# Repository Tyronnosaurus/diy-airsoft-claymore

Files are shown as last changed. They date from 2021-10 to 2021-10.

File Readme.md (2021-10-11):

# DIY Airsoft claymore

## About

This is a remote controlled, motion sensing, BB throwing airsoft Claymore that I developed, built and used on my own matches.
I'm releasing its design on the hope that other makers can enjoy it.

More info and some videos @ https://airsoftdiy.com/3d-printed-airsoft-claymore/

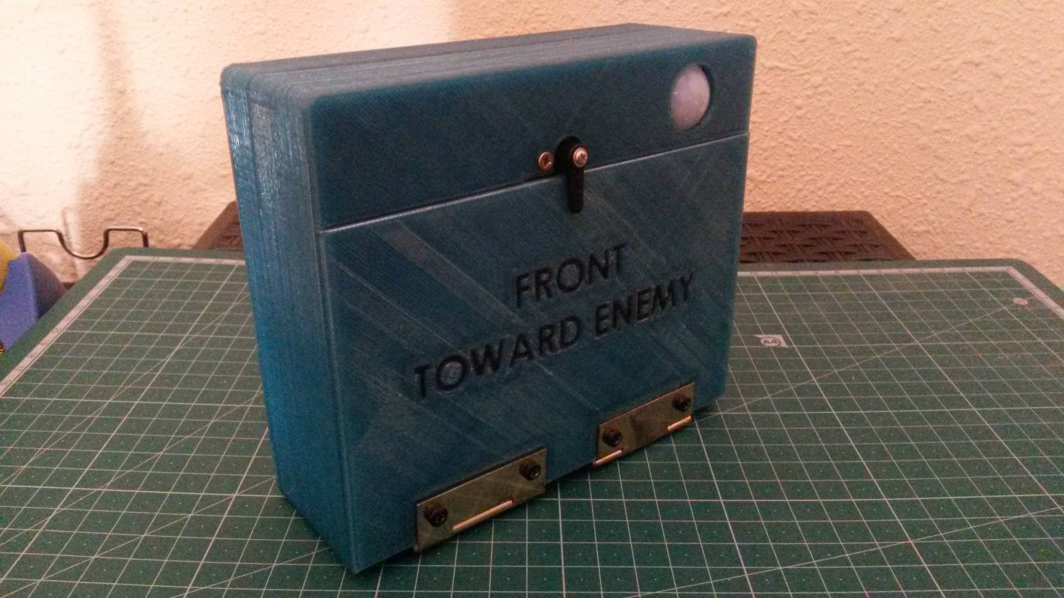
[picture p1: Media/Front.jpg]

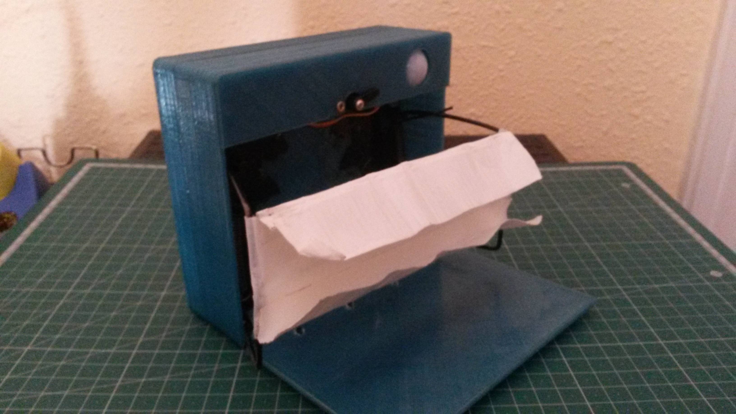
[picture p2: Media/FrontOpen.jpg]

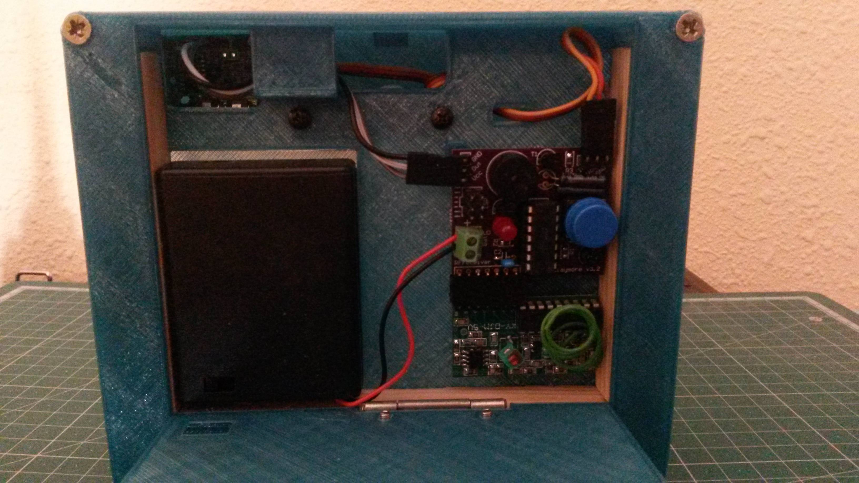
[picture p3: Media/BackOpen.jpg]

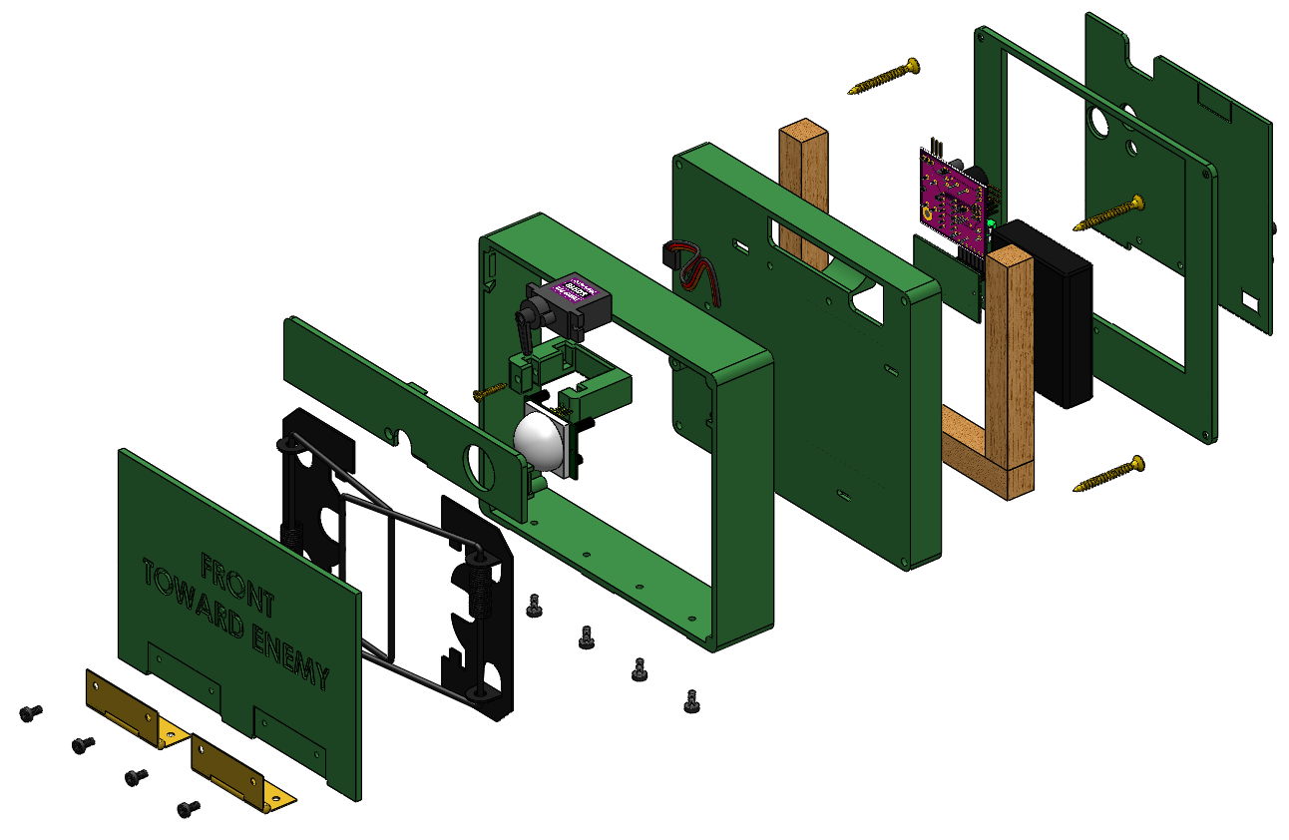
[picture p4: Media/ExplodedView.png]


## Features (for users)
- A doble mousetrap mechanism that shoots BBs forward.
- A motion sensor that triggers when an enemy (or a friend, or you) walks in front.
- Flashing Led and loud piezo in case the victim doesn't realize what hit him.
- A button on the backside to open/close (short press) or activate/deactivate the motion sensor (long press).
- A remote controller with these functions (note the bold initials, which correspond to the remote buttons):
	- **A**ctivate the motion sensor.
	- **B**OOM -> Immediately opens and shoots the BBs.
	- **C**heck range -> Flash Led. Useful if you hide far and aren't sure if the signal will reach. If it's too sunny to see the Led, a long press will also trigger a sound. 
	- **D**eactivate the motion sensor.
- Works on 4xAAA batteries. Very long battery life. While it's not opening or closing, it sleeps and only consumes a few microamperes (even while motion sensor is active).

## Features (for makers)
- Easy to print body. All parts have a flat surface and need no supports.
- Most of the structural integrity comes from 3 internal wood bars. Otherwise it would literally self-destruct due to the force of the rat trap springs.
- Easy to solder PCB. Most components are big and through-hole, with a couple SMD resistors but they're still relatively big.

## Instructions
**At the moment there is no step-by-step tutorial**. If you wish to build your own Claymore, you need to be familiar with:

- 3D printing stl files
- Manufacturing a PCB from gerbers (as in, sending it to a fabhouse)
- Sourcing and soldering electronic components (most are very basic, but ask for help if needed)
- Loading an Arduino program into an ATtiny84 (I recommend using an SPI programmer, since I put a connector on the board)
	
If you want to modify the enclosure and the PCB, you’ll also need to use Solidworks and Altium, respectively.
The firmware is developed in C++ on the Arduino IDE.

## License
Licenced under GPLv3+. Contact the author if you wish to use it under any other license.

    This program is free software: you can redistribute it and/or modify
    it under the terms of the GNU General Public License as published by
    the Free Software Foundation, either version 3 of the License, or
    (at your option) any later version.

    This program is distributed in the hope that it will be useful,
    but WITHOUT ANY WARRANTY; without even the implied warranty of
    MERCHANTABILITY or FITNESS FOR A PARTICULAR PURPOSE.  See the
    GNU General Public License for more details.

    You should have received a copy of the GNU General Public License
    along with this program.  If not, see <http://www.gnu.org/licenses/>.

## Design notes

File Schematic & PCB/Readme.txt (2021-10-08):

This is an Altium project.
Originally made in Altium 16.1.17.
You will need Altium ONLY if you want to edit the board.

You can also grab the exported gerbers in the "Project Outputs" folder and send them to a PCB fabhouse of your choice.

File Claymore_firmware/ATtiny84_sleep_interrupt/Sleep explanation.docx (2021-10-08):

# Bit manipulation

bitSet(Byte,bit) changes a specific bit inside a byte to 1.

bitClear(byte,bit) changes a specific bit inside a byte to 0.

# Two groups of interrupts

…

# PCMSK0 - Pin Change Mask Register 0

Bits 7:0 – PCINT7:0: Pin Change Enable Mask 7:0

Each PCINT7:0 bit selects whether pin change interrupt is enabled on the corresponding I/O pin. If PCINT7:0 is set and the PCIE0 bit in GIMSK is set, pin change interrupt is enabled on the corresponding I/O pin. If PCINT7:0 is cleared, pin change interrupt on the corresponding I/O pin is disabled.

# GIMSK – General Interrupt Mask Register

Bit 4 – PCIE0: Pin Change Interrupt Enable 0

When the PCIE0 bit is set (one) and the I-bit in the Status Register (SREG) is set (one), pin change interrupt 0 is enabled. Any change on any enabled PCINT7:0 pin will cause an interrupt. The corresponding interrupt of Pin Change Interrupt Request is executed from the PCI0 Interrupt Vector. PCINT7:0 pins are enabled individually by the PCMSK0 Register.

# GIFR – General Interrupt Flag Register

Bit 4 – PCIF0: Pin Change Interrupt Flag 0

When a logic change on any PCINT7:0 pin triggers an interrupt request, PCIF becomes set (one). If the I-bit in SREG and the PCIE0 bit in GIMSK are set (one), the MCU will jump to the corresponding Interrupt Vector. The flag is cleared when the interrupt routine is executed. Alternatively, the flag can be cleared by writing a logical one to it.

# SREG – AVR Status Register

Bit 7 – I: Global Interrupt Enable

Must be set for the interrupts to be enabled. The individual interrupt enable control is then performed in separate control registers. If the Global Interrupt Enable Register is cleared, none of the interrupts are enabled independent of the individual interrupt enable settings. The I-bit is cleared by hardware after an interrupt has occurred, and is set by the RETI instruction to enable subsequent interrupts. The I-bit can also be set and cleared by the application with the SEI and CLI instructions, as described in the instruction set reference.

# MCUCR – MCU Control Register

The External Interrupt Control Register A contains control bits for interrupt sense control.

Bits 1:0 – ISC01, ISC00: Interrupt Sense Control 0 Bit 1 and Bit 0

The External Interrupt 0 is activated by the external pin INT0 if the SREG I-flag and the corresponding interrupt mask are set. The level and edges on the external INT0 pin that activate the interrupt are defined in Table 9-2. The value on the INT0 pin is sampled before detecting edges. If edge or toggle interrupt is selected, pulses that last longer than one clock period will generate an interrupt. Shorter pulses are not guaranteed to generate an interrupt. If low level interrupt is selected, the low level must be held until the completion of the currently executing instruction to generate an interrupt.

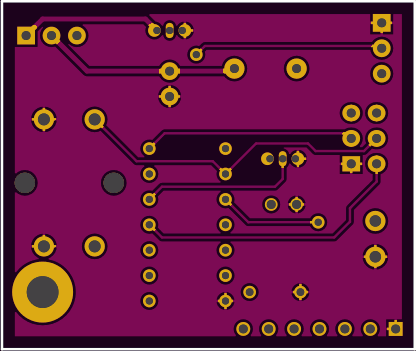
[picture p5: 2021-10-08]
Media/PCB-Bottom.png

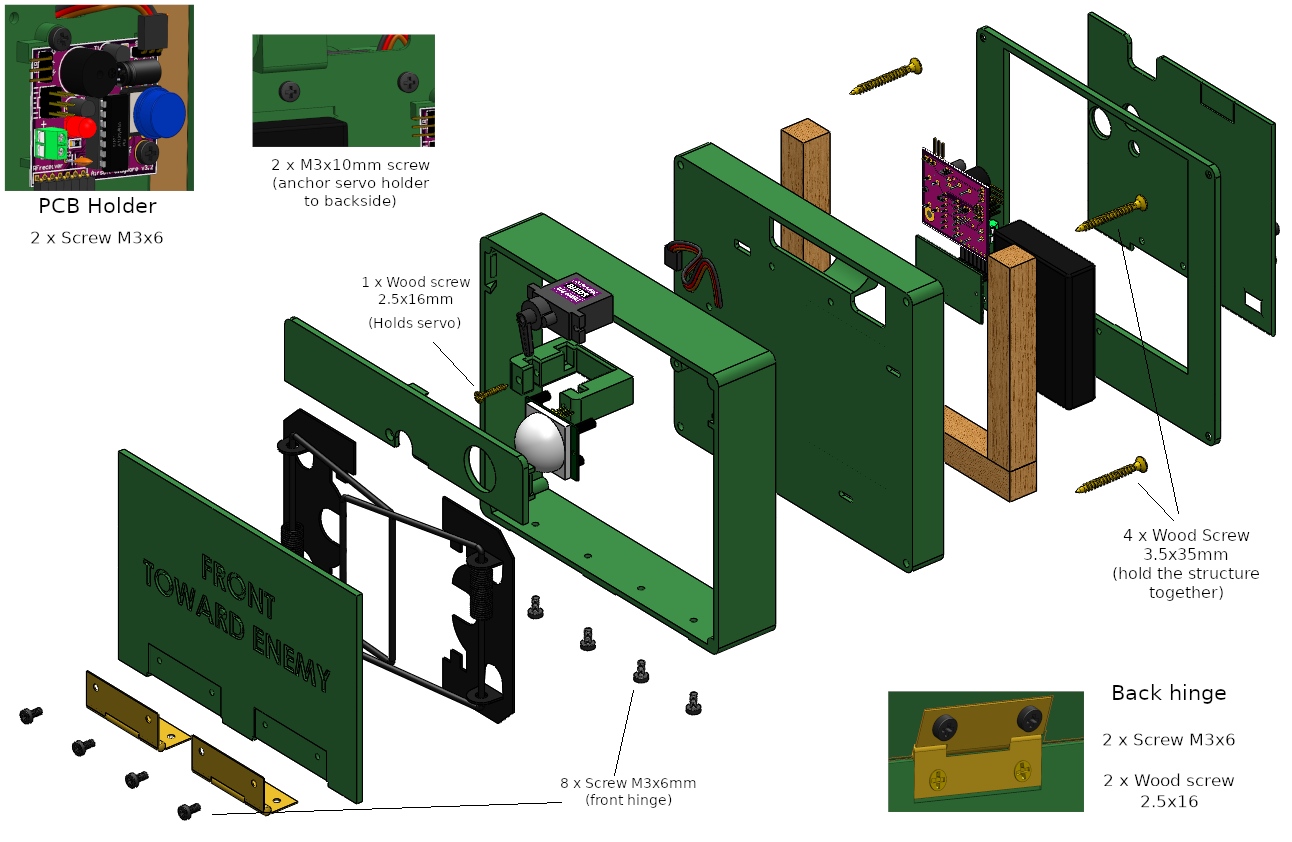
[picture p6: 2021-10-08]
Media/ExplodedView (screws).PNG

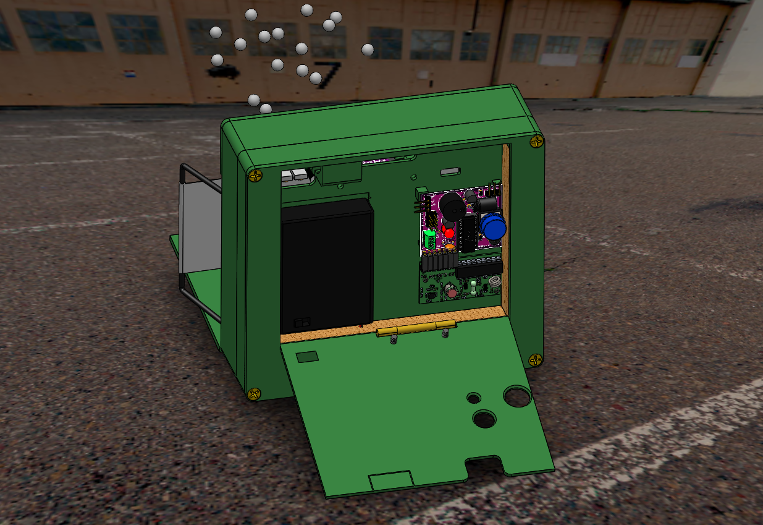
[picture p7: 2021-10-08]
Media/Capture.PNG

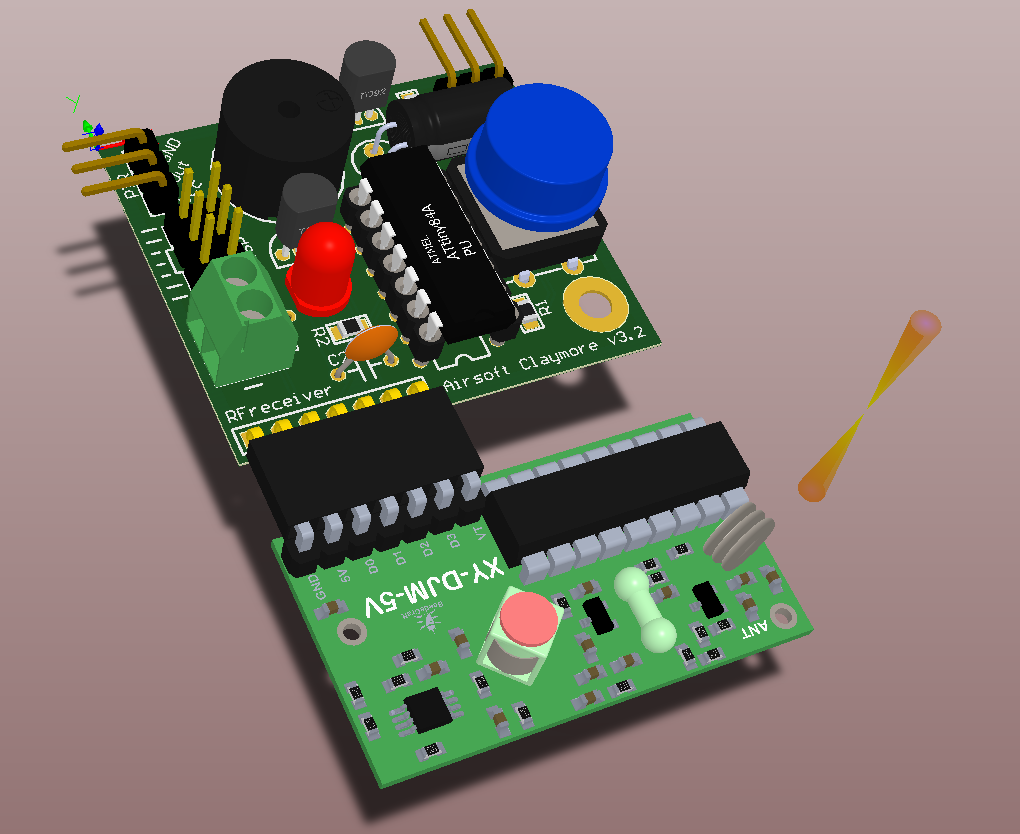
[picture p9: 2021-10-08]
Media/PCB v3.2.PNG

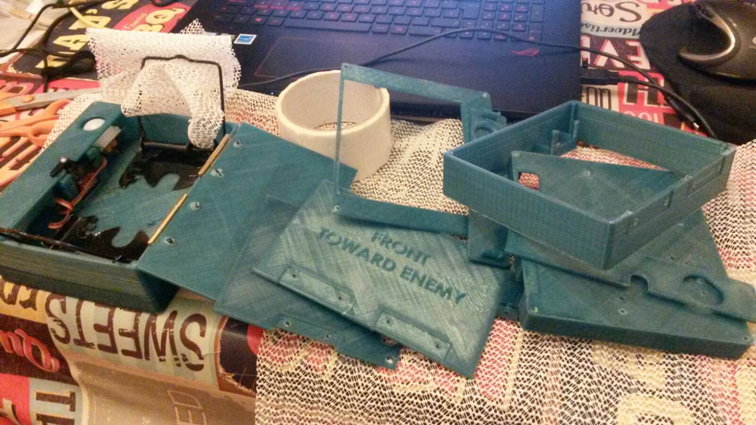
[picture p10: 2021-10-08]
Media/IMG-20161224-WA0004.jpg

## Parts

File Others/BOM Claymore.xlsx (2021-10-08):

Part | Quantity | Price |  | Cost
Mechanical
Mousetrap | 2 | 3.00 € | u | 6.00 €
Big hinge | 2 |  |  | 0.90 € | 34.7
Small hinge | 1 |  |  | 0.70 €
Tape |  |  |  | 0.00 €
Wood log long | 1 |  |  | 0.10 €
Wood log short | 2 |  |  | 0.10 €
Wood screw long |  |  |  | 0.30 €
Wood screw short |  |  |  | 0.30 €
Nut M3 |  |  |  | 0.50 €
Washer | 4 |  |  | 0.20 €
Electronics
Servo | 1 |  |  | 1.00 €
PIR | 1 |  |  | 1.00 €
Buzzer | 1 |  |  | 1.00 €
PCB | 1 |  |  | 6.00 €
Battery Holder 4xAAA | 1 |  |  | 1.00 €
Switch | 1 |  |  | 1.00 €
RF Emitter+Reciever | 1 |  |  | 1.00 €
Terminal | 3 |  |  | 0.30 €
ATMEGA328p | 1 |  |  | 1.20 €
24 DIP Socket | 1 |  |  | 0.50 €
Pushbutton | 1 |  |  | 0.50 €
LED | 1 |  |  | 0.10 €
Resistor | 2 |  |  | 0.10 €
Capacitor 220 uF | 1 |  |  | 0.10 €
Transistor | 2 |  |  | 0.50 €
Pin header female | 14 |  |  | 0.10 €
Dupont cable (PIR connector) | 3 |  |  | 0.10 €
Assorted cable |  |  |  | 0.10 €
AAA Battery | 1 |  |  | 0.00 €
3D printed
Front chassis |  |  |  | 10.00 €
Front cover hinged
Front cover fixed
Servo holder
Back chassis
Back cover hinged
Back cover fixed

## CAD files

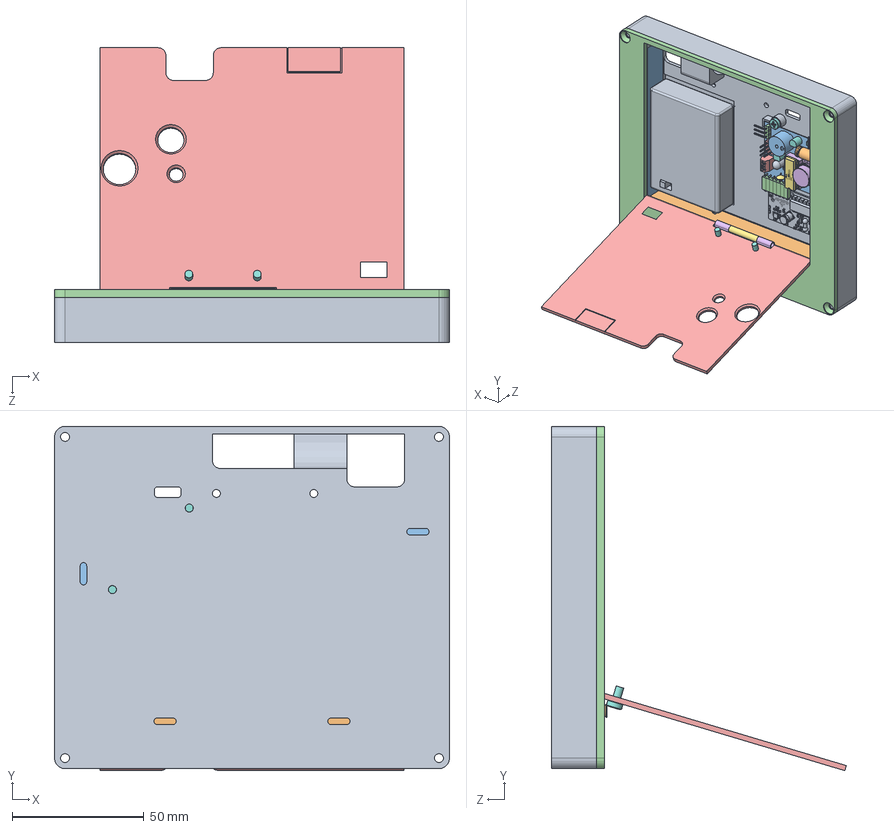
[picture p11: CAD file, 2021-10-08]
3D Model/Claymore - Back half.SLDASM
150.0 x 130.8 x 111.9 mm
Back Chassis
Wood log 14x14 Long
Wood log 14x14 Short x 2
Back cover (fixed)
Back cover (hinged)
Hinge 39x24 - Piece 1
Hinge 39x24 - Piece 2
Screw 3x6 Philips x 4
4xAAA (with cover+switch)
Screw 2.5x16 Philips x 2
PCB_Substrate
Male_pin_header_90º_1x1 x 6
Male_pin_header_1x1 x 6
12mm Pushbutton
Ceramic_capacitor_5mm
TO-92 x 2
LED_5_mm_Red
Electrolytic capacitor 6.5x11 - Horizontal 2
Piezo 12mm
Pin_Header_Female_1x1_RightAngle x 7
Terminal block 2x0.14in
DIP Socket 14pin
ATtiny84
Resistor SMD 0805 x 3
RF_433MHz_Receiver_(RemoteControl)

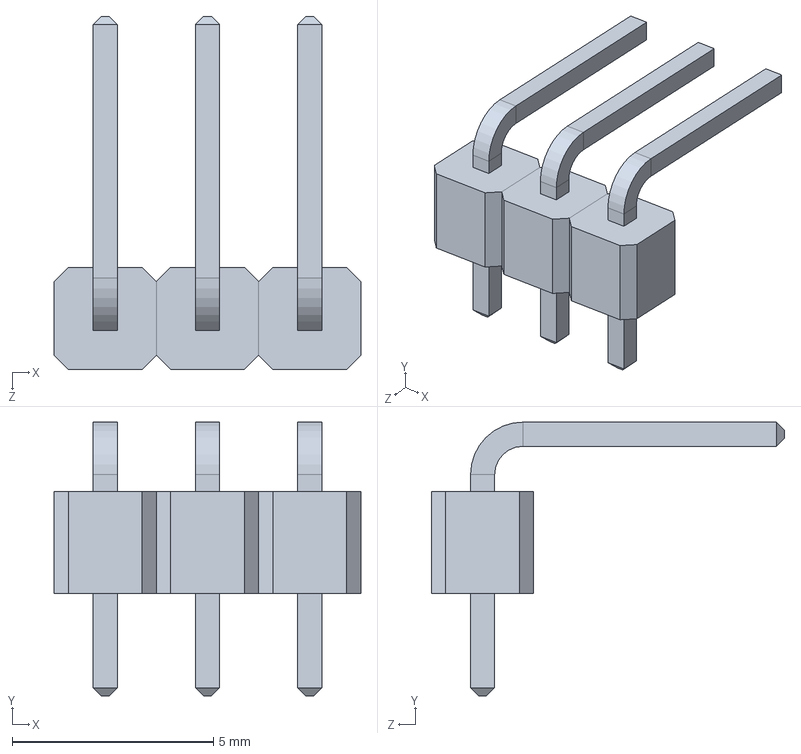
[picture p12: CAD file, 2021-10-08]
3D Model/Electrical_components/Components/Pin header - male/Male_pin_header_90º_3x1.SLDASM
7.62 x 6.80 x 8.77 mm
Male_pin_header_90º_1x1 x 3

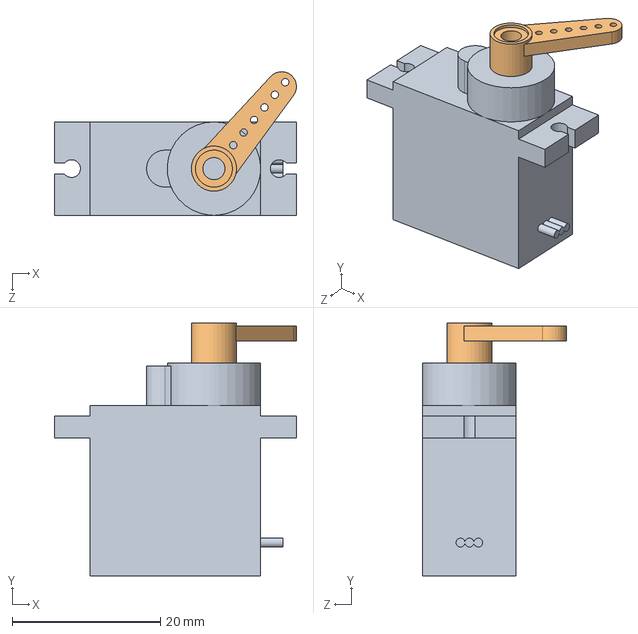
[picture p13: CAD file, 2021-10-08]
3D Model/Electrical_components/Components/Servo/Servo.SLDASM
32.6 x 34.1 x 19.4 mm
Servo - Main body
Servo - Arm 1

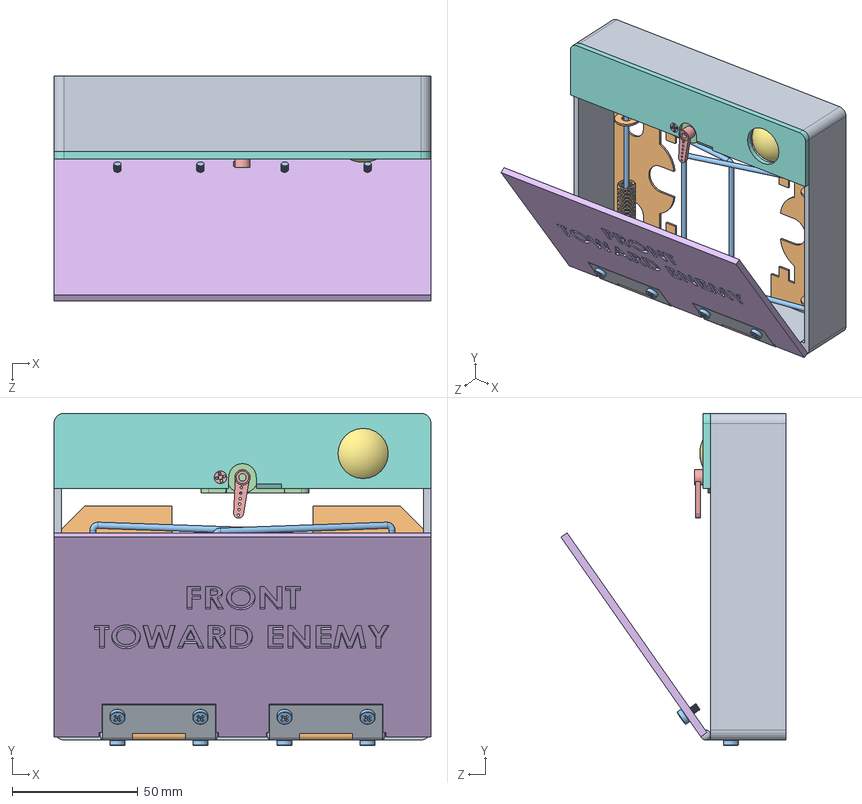
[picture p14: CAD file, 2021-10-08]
3D Model/Claymore - Front half.SLDASM
150.0 x 132.3 x 89.6 mm
Front Chassis
Rat trap - Base x 2
Rat trap - Filament x 2
Servo - Main body
Servo - Arm 1
Front cover (hinged)
PIR Sensor
Front cover (top)
Hinge 45x32 - Piece 1 x 2
Hinge 45x32 - Piece 2 x 2
Screw 3x6 Philips x 8
Servo holder
Screw 2.5x16 Philips

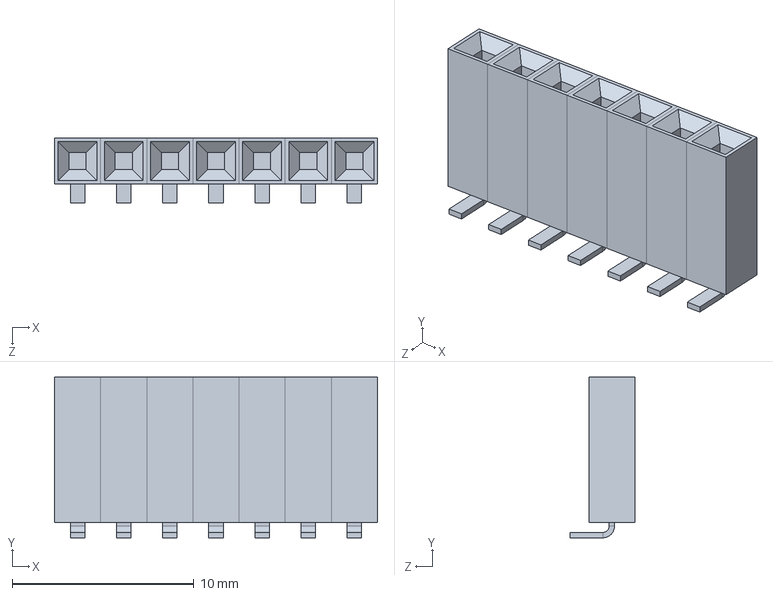
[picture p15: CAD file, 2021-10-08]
3D Model/Electrical_components/Components/Pin header - female/Pin_Header_Female_1x7_RightAngle.SLDASM
17.8 x 8.85 x 3.57 mm
Pin_Header_Female_1x1_RightAngle x 7

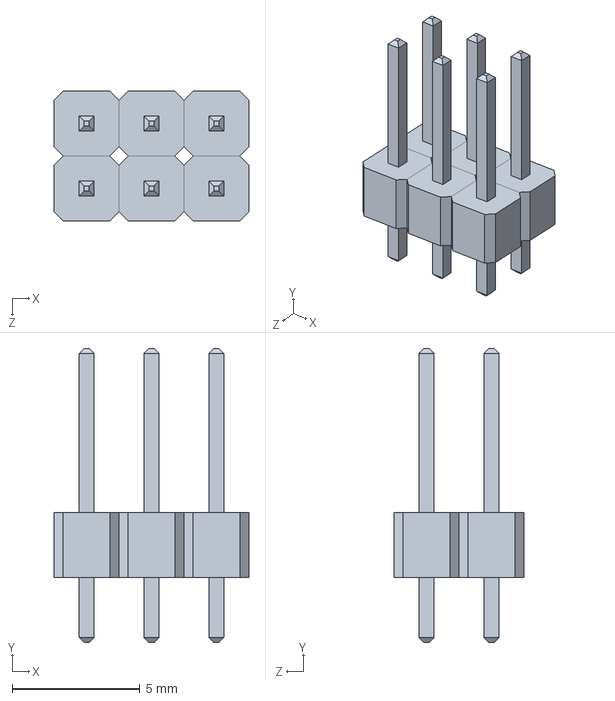
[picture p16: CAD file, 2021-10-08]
3D Model/Electrical_components/Components/Pin header - male/Male_pin_header_2x3.SLDASM
7.62 x 11.5 x 5.08 mm
Male_pin_header_1x1 x 6

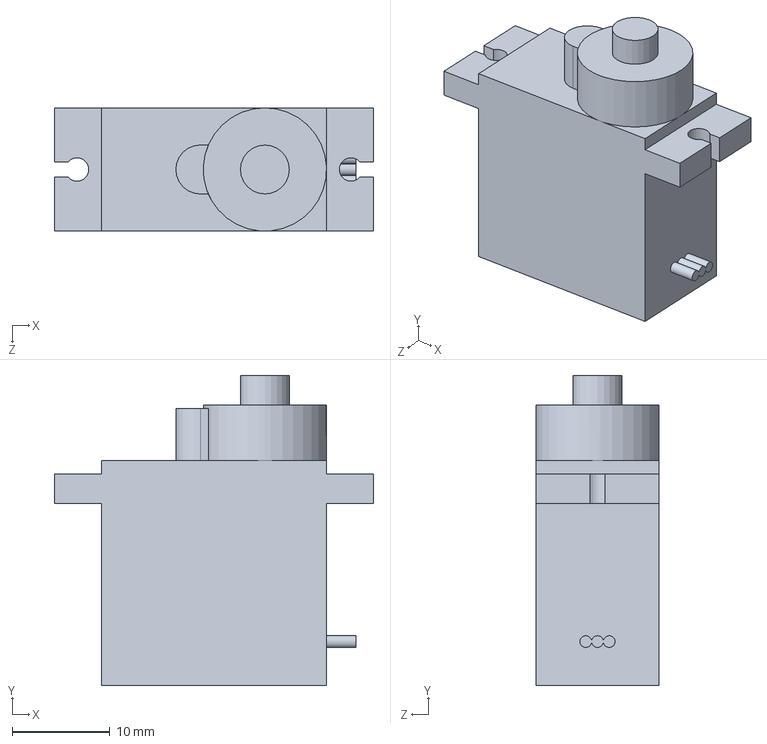
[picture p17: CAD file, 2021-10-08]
3D Model/Electrical_components/Components/Servo/Servo - Main body.SLDPRT
32.6 x 31.7 x 12.6 mm

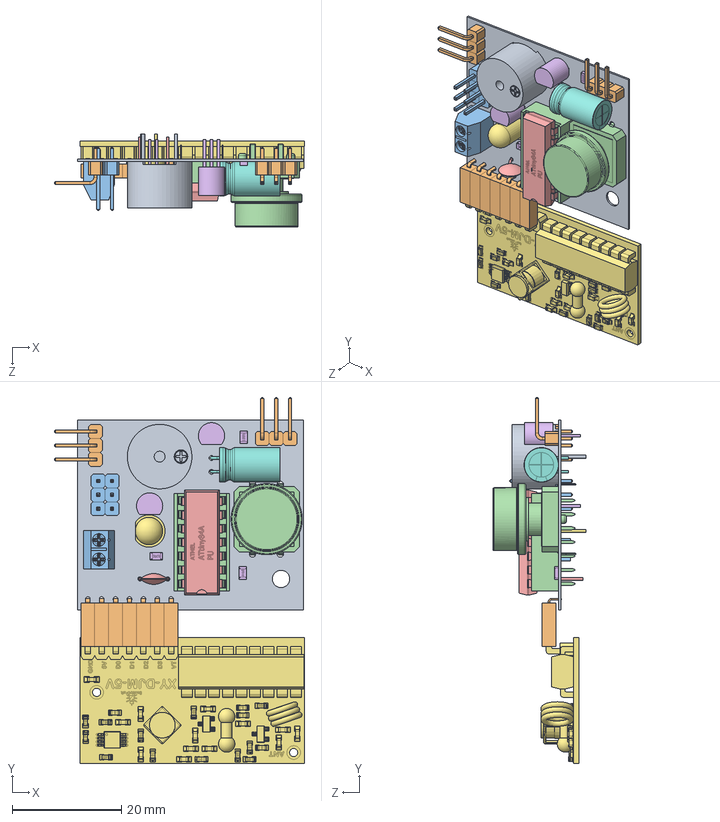
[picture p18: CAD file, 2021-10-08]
3D Model/Electrical_components/PCB_Populated.SLDASM
45.7 x 66.9 x 17.0 mm
PCB_Substrate
Male_pin_header_90º_1x1 x 6
Male_pin_header_1x1 x 6
12mm Pushbutton
Ceramic_capacitor_5mm
TO-92 x 2
LED_5_mm_Red
Electrolytic capacitor 6.5x11 - Horizontal 2
Piezo 12mm
Pin_Header_Female_1x1_RightAngle x 7
Terminal block 2x0.14in
DIP Socket 14pin
ATtiny84
Resistor SMD 0805 x 3
RF_433MHz_Receiver_(RemoteControl)

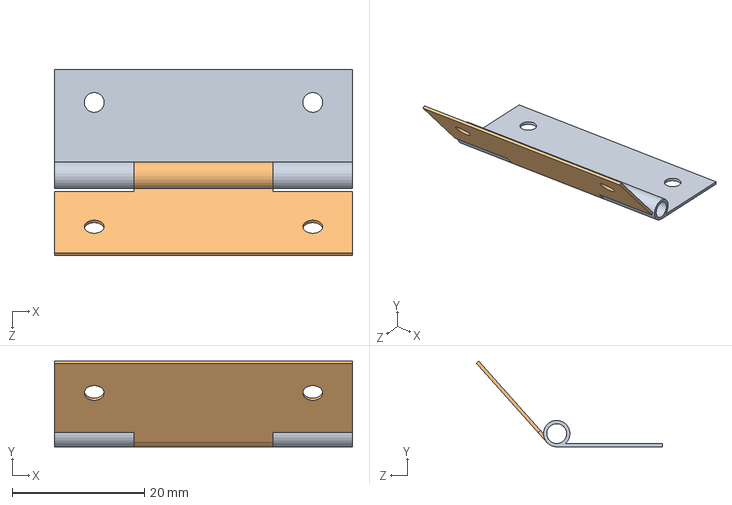
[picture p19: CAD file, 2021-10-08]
3D Model/Mechanical/Hinges/Hinge 45x32/Hinge 45x32.SLDASM
45.0 x 12.9 x 28.1 mm
Hinge 45x32 - Piece 1
Hinge 45x32 - Piece 2

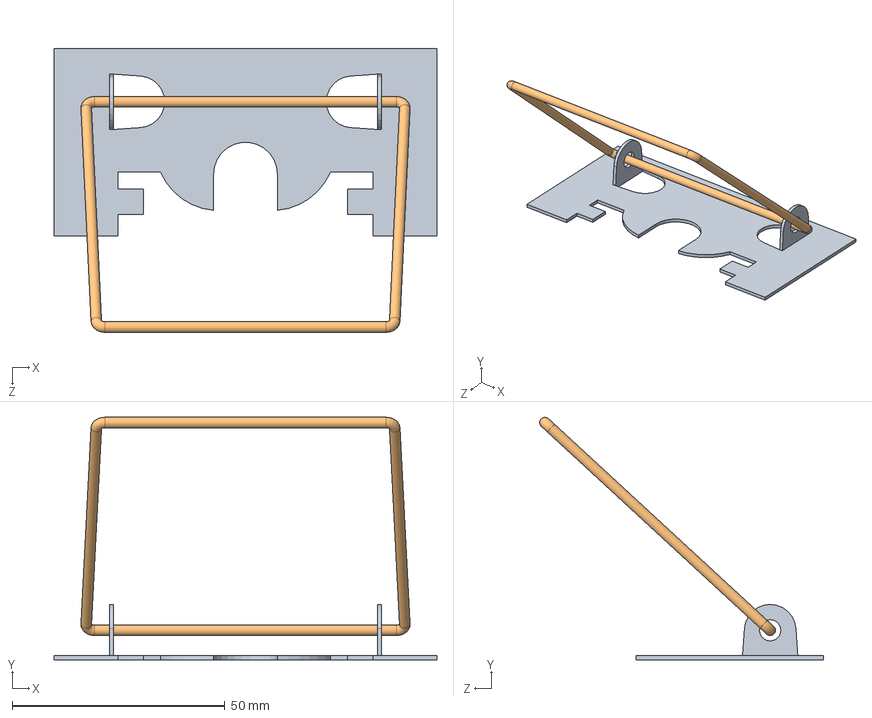
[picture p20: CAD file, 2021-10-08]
3D Model/Mechanical/Rat trap/Rat trap.SLDASM
90.0 x 57.0 x 66.7 mm
Rat trap - Base
Rat trap - Filament

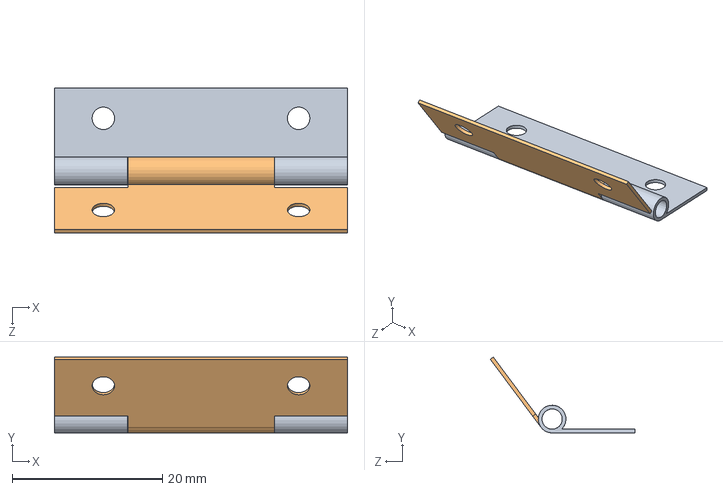
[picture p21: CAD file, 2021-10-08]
3D Model/Mechanical/Hinges/Hinge 39x24/Hinge 39x24.SLDASM
39.0 x 10.1 x 19.2 mm
Hinge 39x24 - Piece 1
Hinge 39x24 - Piece 2

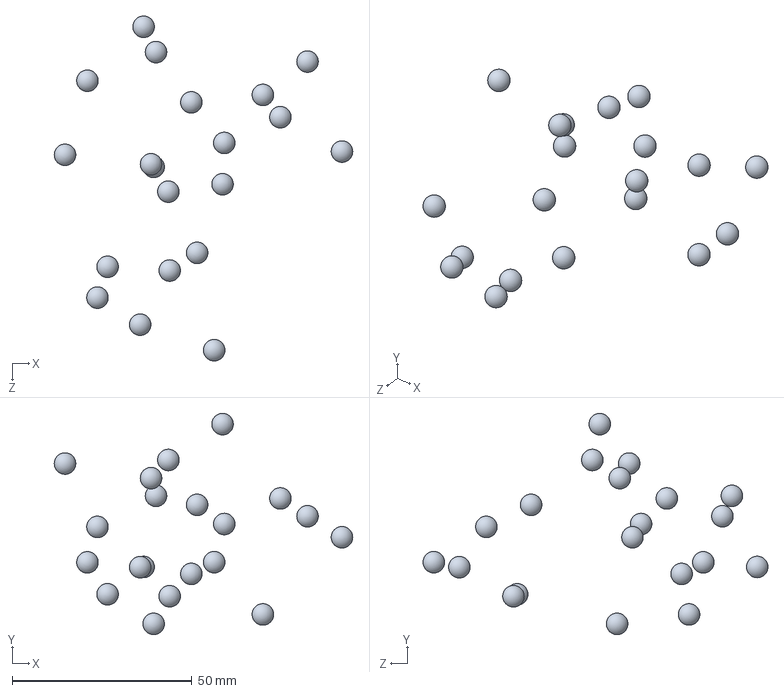
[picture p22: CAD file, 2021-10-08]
3D Model/Mechanical/BB Spread.SLDASM
83.0 x 61.5 x 95.9 mm
BB x 20

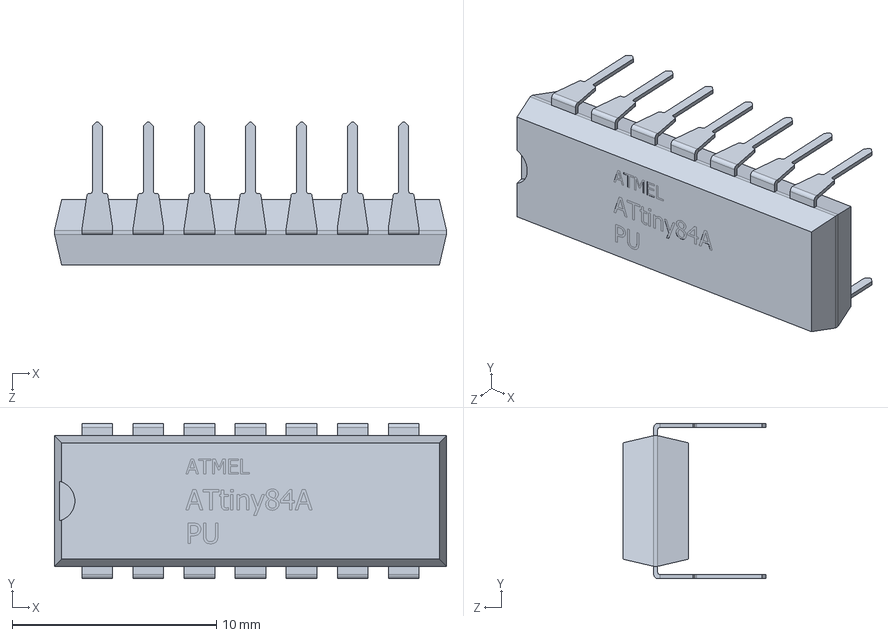
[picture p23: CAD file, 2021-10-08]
3D Model/Electrical_components/Components/ATtiny84.SLDPRT
19.2 x 7.60 x 7.00 mm

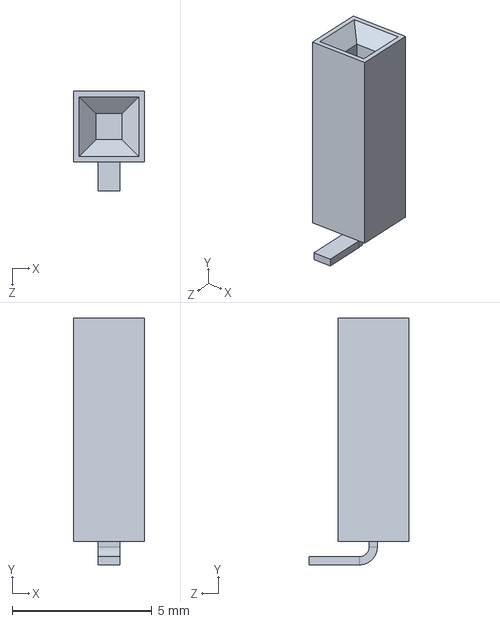
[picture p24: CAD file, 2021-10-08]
3D Model/Electrical_components/Components/Pin header - female/Pin_Header_Female_1x1_RightAngle.SLDPRT
2.54 x 8.85 x 3.57 mm

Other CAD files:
3D Model/Electrical_components/PCB_Substrate.SLDPRT
3D Model/Mechanical/BB.SLDPRT
3D Model/Mechanical/Chassis/Front Chassis.SLDPRT
3D Model/Mechanical/Covers/Front cover (hinged).SLDPRT
3D Model/Electrical_components/Components/12mm Pushbutton.sldprt
3D Model/Electrical_components/Components/4xAAA (with cover+switch).SLDPRT
3D Model/Electrical_components/Components/Ceramic_capacitor_5mm.sldprt
3D Model/Electrical_components/Components/DIP Socket 14pin.SLDPRT
3D Model/Electrical_components/Components/Electrolytic capacitor 6.5x11 - Horizontal 2.SLDPRT
3D Model/Electrical_components/Components/LED_5_mm_Red.sldprt
3D Model/Electrical_components/Components/PIR Sensor.SLDPRT
3D Model/Electrical_components/Components/Piezo 12mm.SLDPRT
3D Model/Electrical_components/Components/Pin header - male/Male_pin_header_1x1.sldprt
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

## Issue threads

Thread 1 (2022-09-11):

Weak layer adhesion in front (where long screws don't reach)

Tyronnosaurus, 2022-09-11:
The Claymore has 4 long wood screws that go from back to front and hold it together so that print layers don't separate. However, they don't reach all the way to the front.

On those few millimetres, the only thing holding the force of the mousetraps is the adhesion between layers. On the bottom there's 4 holes where the hinges are screwed. Those holes are weak points from where the whole layer can snap:

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

Ideally, the screws should reach from end to end so that all layers are held by screws.

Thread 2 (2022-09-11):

Battery holder needs to be held with something better than glue

Tyronnosaurus, 2022-09-11:
Glue doesn't adhere well enough in there.

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

Possible solution 1: Hot glue.
Possible solution 2: Redesign the back plate (make the fixed part bigger and the hinged part smaller) so that the battery holder has to be pushed in and then it slides to the left and somehow locks in.

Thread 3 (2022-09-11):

Lock mechanism for back cover

Tyronnosaurus, 2022-09-11:
The hinged back cover was originally designed with no 'lock' mechanism. Somehow the starts aligned and the tolerance of the 3D prints made it lock in perfectly because it was slightly bigger than the hole. However, after some time the edge wore down and it no longer locks in, so I just use a piece of tape.

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

It needs a lock mechanism. Possible solutions:
- Change in the 3D print: add some bumps and holes on the parts.
- Some comercial solution like in cupboard doors (but much smaller).
- Magnets.

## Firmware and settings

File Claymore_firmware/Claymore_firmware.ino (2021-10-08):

#include <avr/sleep.h>
#include <avr/power.h>    // Power management



///////////////////////////////////////////////////////////
////CONSTANTS//////////////////////////////////////////////
///////////////////////////////////////////////////////////

////BUTTONS
const int BUTTONpin = 4;  //Will be used for an interrupt
const int SHORTPRESSTIME = 800;  //Max milliseconds to consider press as short
const int LONGPRESSTIME = 2000;  //Min milliseconds to consider press as long

///PIR SENSOR
const int PIRpin = 7;
const int CALIBRTIME = 10;  //Seconds to allow the PIR sensor to calibrate after setting the mine (10+ recommended)

////SIGNAL LEDs AND PIEZO
const int LEDpin = 5;
const int PIEZOpin = 8;

////SERVO
const int SERVOpin = 10;
const int SERVOPOWERpin = 9;
const int angleOpen = 140;
const int angleClosed = 30;

////RF RECEIVER
const int RF_A_pin = 1;   //Receiver pin D2
const int RF_B_pin = 3;   //Receiver pin D0
const int RF_C_pin = 0;   //Receiver pin D3
const int RF_D_pin = 2;   //Receiver pin D1


                        
                        
///////////////////////////////////////////////////////////
////GLOBAL VARIABLES///////////////////////////////////////
///////////////////////////////////////////////////////////

////SERVO
boolean servoIsOpen;  //Tracks servo position. Starts closed


////State of the finite state machine
enum state_type{IDLE_SERVO_CLOSED, IDLE_SERVO_OPEN, CALIBRATING, ARMED};
state_type state = IDLE_SERVO_CLOSED;




///////////////////////////////////////////////////////////
////SETUP//////////////////////////////////////////////////
///////////////////////////////////////////////////////////
void setup()
{
  ////BUTTON
  pinMode(BUTTONpin, INPUT_PULLUP);  // Configure the pin as an input, and turn on the pullup resistor.
  
  //PIR Sensor
  pinMode(PIRpin, INPUT);
  
  //SERVO
  pinMode(SERVOpin,OUTPUT);
  pinMode(SERVOPOWERpin,OUTPUT);
  
  ////LEDS & PIEZO
  pinMode(LEDpin,OUTPUT);
  pinMode(PIEZOpin,OUTPUT);

  ////RF RECIEVER
  pinMode(RF_B_pin,INPUT);
  pinMode(RF_D_pin,INPUT);
  pinMode(RF_C_pin,INPUT);
  pinMode(RF_A_pin,INPUT);
  
  //Serial
  //Serial.begin(9600);

  PowerOnSignal();
  delay(100);
}



///////////////////////////////////////////////////////////
///////LOOP////////////////////////////////////////////////
///////////////////////////////////////////////////////////
void loop()
{
  switch (state)
  {

    case IDLE_SERVO_CLOSED:
    { 
      //Serial.println("----------------------------------\nState: IDLE_SERVO_CLOSED");
  
      GoToSleep(); //Goes to sleep until input is detected (button or remote)
  
      delay(5);
      
      //The uC wakes up. Check if user made a short or long button press
      if (digitalRead(BUTTONpin)==LOW)
      {
        //Serial.print("Button pressed: ");
        long pressLength = GetPressLength();  //The button has been pressed. Check how long it's been pressed
       
        if (pressLength < SHORTPRESSTIME)
        {
          //Serial.println("Short");
          openServo();
          state = IDLE_SERVO_OPEN;
        }
        else
        {
          //Serial.println("Long");
          CalibratingSignal();
          state = CALIBRATING;
        }
      }

      else if (digitalRead(RF_A_pin)==HIGH)
      {
        CalibratingSignal();
        state = ARMED;        
      }
      else if (digitalRead(RF_B_pin)==HIGH)
      {
        //Serial.println("Short");
        openServo();
        state = IDLE_SERVO_OPEN;
      }
      else if (digitalRead(RF_C_pin)==HIGH)
      {
        CheckRange();
      }
      
      break;
    }

    /////////////////////////////////////////////////////////////////////////////////////////////////////////

    case IDLE_SERVO_OPEN:
    {
      //Serial.println("----------------------------------\nState: IDLE_SERVO_OPEN");
      GoToSleep(); //Goes to sleep until input is detected (button or remote)

      //The uC wakes up. Check if user made a short or long button press
      if (digitalRead(BUTTONpin)==LOW)
      {  
        //Serial.print("Button pressed: ");
        long pressLength = GetPressLength();  //The button has been pressed. Check how long it's been pressed
        
        if (pressLength < SHORTPRESSTIME)
        {
          //Serial.println("Short");
          closeServo();
          state = IDLE_SERVO_CLOSED;
        }
        else
        {
          //Serial.println("Long");
          closeServo();
          CalibratingSignal();
          state = CALIBRATING;
        }
      }

      else if (digitalRead(RF_B_pin)==HIGH)
      {
        closeServo();
        state = IDLE_SERVO_CLOSED;
      }
      else if (digitalRead(RF_C_pin)==HIGH) 
      {
        CheckRange();
      }
      
      break;
    }

    /////////////////////////////////////////////////////////////////////////////////////////////////////////

    case CALIBRATING:
    {
      delay(1000);  //Give time to release button

      //Wait some time while the PIR is calibrating, but still check for any user input
      //Additionally, don't finish callibration until the PIR has gone low (or else there's a few seconds 
      //after entering ARMED mode when it isn't really able to detect enemies
      boolean deactivated = false;
      long start = millis();
      while((millis()-start < CALIBRTIME*1000) && !(digitalRead(PIRpin)) && !deactivated)
      {
        if(digitalRead(BUTTONpin)==LOW) //Button pressed: Disarm explosive
        {
          deactivated = true;
          DisarmedSignal();
          state = IDLE_SERVO_CLOSED;          
        }
        else if(digitalRead(RF_D_pin)==HIGH)  //Remote D (Deactivate) pressed
        {
          deactivated = true;
          DisarmedSignal();
          state = IDLE_SERVO_CLOSED;
        }
        else if(digitalRead(RF_B_pin)==HIGH)  //Remote B (Boooom!) pressed
        {
          Explode();
          state = IDLE_SERVO_OPEN;
        }

        delay(5);
      }

      if(!deactivated)
      {
        //Calibration finished. Claymore now live and dangerous!
        EndOfCalibrationSignal();
        state = ARMED;
      }
      
      break;
    }


    /////////////////////////////////////////////////////////////////////////////////////////////////////////

    case ARMED:
    {
      //Serial.println("\n----------------------------------\nState: ARMED");
      GoToSleep();

      //Detected PIR --> Explode
      if(digitalRead(PIRpin)==HIGH)
      {
        Explode();
        state = IDLE_SERVO_OPEN;
      }

      //Detected button --> Deactivate
      else if(digitalRead(BUTTONpin)==LOW)
      { 
        //Serial.println("\nButton pressed: Disarming explosive");
        DisarmedSignal();
        state = IDLE_SERVO_CLOSED;
      }

      
      //Detected remote
      else if(digitalRead(RF_B_pin)==HIGH)
      {
        Explode();
        state = IDLE_SERVO_OPEN;
      }
      else if(digitalRead(RF_C_pin)==HIGH)
      {
        CheckRange();
      }
      else if(digitalRead(RF_D_pin)==HIGH)
      {
        //Serial.println("\nRemote 'D' button pressed: Disarming explosive");
        DisarmedSignal();
        state = IDLE_SERVO_CLOSED;
      }
      break;
    }

    /////////////////////////////////////////////////////////////////////////////////////////////////////////
    
    default:
      break;

  }

}




///////////////////////////////////////////////////////////
////FUNCTIONS//////////////////////////////////////////////
///////////////////////////////////////////////////////////

//The Tone library is incompatible with ATtiny microcontrollers, so I use this function to play notes on the piezo
void PlayNotePiezo(int freq, int duration)
{
  int halfT = 0.5*1000000/freq;

  long start = millis();
  while(millis()-start < duration)
  {
    digitalWrite(PIEZOpin,HIGH);
    delayMicroseconds(halfT);
    digitalWrite(PIEZOpin,LOW);
    delayMicroseconds(halfT);
  }
}


//Makes a signal when the device is powered on and starts servo at closed position
void PowerOnSignal()
{
  
  digitalWrite(LEDpin,HIGH);
  PlayNotePiezo(300,20);
  delay(500);
  digitalWrite(LEDpin,LOW); 

  closeServo();
  //Serial.println("Program start");
}



//Put the IC to sleep until it receives an external signal from the button or the remote. Also from the PIR when Claymore is armed.
void GoToSleep()
{
  delay(50);
  //Serial.println("Preparing sleep");
  delay(50);

  //Enable pin change interrupt on selected pins
  bitClear(GIFR,PCIF0);   //Clear any outstanding interrupts (recommended)
  bitSet(GIMSK,PCIE0);    //Enable pin change interrupts
  bitSet(PCMSK0,PCINT4);  //Enable interrupt on Pushbutton pin
  if(state==ARMED) bitSet(PCMSK0,PCINT7);  //Enable interrupt on PIR pin
  bitSet(PCMSK0,PCINT0);
  bitSet(PCMSK0,PCINT1);
  bitSet(PCMSK0,PCINT2);
  bitSet(PCMSK0,PCINT3);
  
  //Disable ADC to save energy
  ADCSRA = 0;
 
  set_sleep_mode(SLEEP_MODE_PWR_DOWN);

  power_all_disable();  // power off ADC, Timer 0 and 1, serial interface
  sleep_enable();

 /*
  //Do not interrupt before we go to sleep, or the ISR will detach interrupts and we won't wake up.
  noInterrupts();
 
  //Attach interrupt to a pin  
  attachPinChangeInterrupt(BUTTONpin, Wake, FALLING);
  attachPinChangeInterrupt(RF_VTpin, Wake, RISING);
  if (state == ARMED) attachPinChangeInterrupt(PIRpin, Wake, RISING);
  
  //Turn off brown-out enable in software
  //BODS must be set to one and BODSE must be set to zero within four clock cycles
  MCUCR = bit(BODS) | bit(BODSE);
  //The BODS bit is automatically cleared after three clock cycles
  MCUCR = bit(BODS);
  */

  sleep_cpu();
  //Sleep happens here
  //When the interrupt is triggered, wake up, execute ISR function and continue program execution from here                             
  sleep_disable();   
  power_all_enable();    // power everything back on
}


ISR(PCINT0_vect) 
{
 //Do nothing
}



//Tracks how long the button has been pressed. If it has been pressed long enough for a long press, automatically returns
long GetPressLength()
{  
  long pressLength = 0;
  long previousTime = millis();
  while((digitalRead(BUTTONpin)==LOW)&&(pressLength<LONGPRESSTIME)){
    pressLength += millis() - previousTime;
    previousTime = millis();
    delay(10);
  }
  return(pressLength);
}



void openServo()
{
  int pulseDuration = map(angleOpen, 0, 180, 500, 2400);

  digitalWrite(SERVOPOWERpin,HIGH);
  delay(10);
  long now = millis();
  while(millis()-now < 500)
  {
    digitalWrite(SERVOpin,HIGH);
    delayMicroseconds(pulseDuration);
    digitalWrite(SERVOpin,LOW);
    delay(20);
  }
  //Serial.println("Opening servo");
  servoIsOpen = true;
  digitalWrite(SERVOPOWERpin,LOW);
}


void closeServo()
{
  int pulseDuration = map(angleClosed, 0, 180, 500, 2400);

  digitalWrite(SERVOPOWERpin,HIGH);
  delay(10);
  long now = millis();
  while(millis()-now < 500)
  {
    digitalWrite(SERVOpin,HIGH);
    delayMicroseconds(pulseDuration);
    digitalWrite(SERVOpin,LOW);
    delay(20);
  }
  //Serial.println("Closing servo");
  servoIsOpen = false;
  digitalWrite(SERVOPOWERpin,LOW);
}



void EndOfCalibrationSignal()
{
  digitalWrite(LEDpin,HIGH);
  PlayNotePiezo(1000,10);
  delay(300);
  digitalWrite(LEDpin,LOW);
}



//Closes the servo and makes a signal to indicate the Claymore will soon be armed and dangerous
void CalibratingSignal()
{
  PlayNotePiezo(500,20);
  delay(50);
  PlayNotePiezo(1200,15);

  for(int i=0;i<20;i++)
  {
    digitalWrite(LEDpin,HIGH);
    delay(50);
    digitalWrite(LEDpin,LOW);
    delay(50);
  }
}



//Makes a signal to indicate the Claymore is now loaded but idle
void DisarmedSignal()
{
  PlayNotePiezo(1200,20);
  delay(50);
  PlayNotePiezo(500,15);

  digitalWrite(LEDpin,HIGH);
  delay(500);
  digitalWrite(LEDpin,LOW);
}



void Explode()
{
  openServo();
  
  for(int i=0;i<4;i++)
  {
    digitalWrite(LEDpin,HIGH);
    PlayNotePiezo(1500,300);
    digitalWrite(LEDpin,LOW);
    delay(150);
    
    digitalWrite(LEDpin,HIGH);
    PlayNotePiezo(500,300);
    digitalWrite(LEDpin,LOW);
    delay(150);
  }
}




//Used when the user wants to check if the remote is in or out of range
void CheckRange()
{
    const int TIME = 4000;
    const int PERIOD = 1000;
    
    boolean audioFeedback = false;
    
    long start = millis();
    while(millis()-start < TIME)
    {
      //Update the LED's PWM value to make a heartbeat pattern
      analogWrite(LEDpin,128+127*cos(2*PI/PERIOD*millis()));  //Sets the LED's brightness following a heartbeat pattern

      //If the remote is held down for some seconds, also use the buzzer   
      if((millis()-start > TIME/2) && (digitalRead(RF_C_pin)==HIGH) && !audioFeedback)
      {
        for(int i=0;i<2;i++)
        {
           PlayNotePiezo(1000,10);
           delay(50);
        }
        audioFeedback = true;
      }
    }

  digitalWrite(LEDpin,LOW);
}

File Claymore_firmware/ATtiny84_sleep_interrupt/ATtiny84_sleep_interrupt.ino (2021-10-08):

// ATMEL ATTINY 25/45/85


#include <avr/sleep.h>    // Sleep Modes
#include <avr/power.h>    // Power management

const byte LED = 5;
const byte SWITCH = 4;  //If you change this, you also have to change the 



void setup ()
{
  pinMode (LED, OUTPUT);
  pinMode (SWITCH, INPUT);
  digitalWrite (SWITCH, HIGH);  // internal pull-up

  
  //Enable pin change interrupt on selected pins
  /*
  Interrupts are separated in two groups. Depending on which you use you'll have to change the names of these registers:
  PCINT0...7  -> Use PCMSK0, PCIF0 and PCIE0
  PCINT8...10 -> Use PCMSK1, PCIF1 and PCIE1
  */
  bitClear(GIFR,PCIF0);   //Clear any outstanding interrupts (recommended)
  bitSet(GIMSK,PCIE0);    //Enable pin change interrupts
  bitSet(PCMSK0,PCINT4);  //Enable interrupt on a specific pin
}


void loop ()
{
  for(int i=0; i<5; i++)
  {
    digitalWrite (LED, HIGH);
    delay (1000); 
    digitalWrite (LED, LOW);
    delay (500);
  }
  goToSleep ();
}



void goToSleep ()
{
  set_sleep_mode(SLEEP_MODE_PWR_DOWN);
  ADCSRA = 0;            // turn off ADC
  power_all_disable ();  // power off ADC, Timer 0 and 1, serial interface
  sleep_enable();
  sleep_cpu();
  //Sleep happens here
  //When the interrupt is triggered, wake up, execute ISR function and continue program execution from here                             
  sleep_disable();   
  power_all_enable();    // power everything back on
}


/*
 Interrupt service routine. Executes on wakeup from sleep.
 Do not use timer or delays here. The argument can be either of thes:
  PCINT0_vect: when using interrupts 0...7
  PCINT1_vect: when using interrupts 8...10
 */
ISR(PCINT0_vect) 
{
 // do something interesting here
}

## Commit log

2021-10-08 Started tracking full project on git
    [12mm Pushbutton.sldprt, 4xAAA (with cover+switch).SLDPRT, ATtiny84.SLDPRT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]
2021-10-11 Added accidentally gitignored gerbers
    [PCB1.GBL, PCB1.GBO, PCB1.GBS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]
